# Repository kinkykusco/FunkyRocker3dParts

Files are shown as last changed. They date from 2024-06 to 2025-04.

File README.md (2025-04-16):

# Overview

The Funky Rocker (FR for short) is a DIY sex rocker.  [The plans are for sale from the designer here for a fair price.](http://www.funkyrocker.com)  The FR is a quality design, but is definitely designed without much regard to making it easy to build, or in keeping costs down in terms of parts. The original FR plans require a high degree of accuracy in woodworking, which can be extra challenging with the smaller parts. I switched many of the parts to being 3d printed rather then cut from MDF. After eight months and much use, the 3d printed parts have held up great.  Below are a couple photos of my finished rocker - can you tell which parts are 3d printed? 
<br>
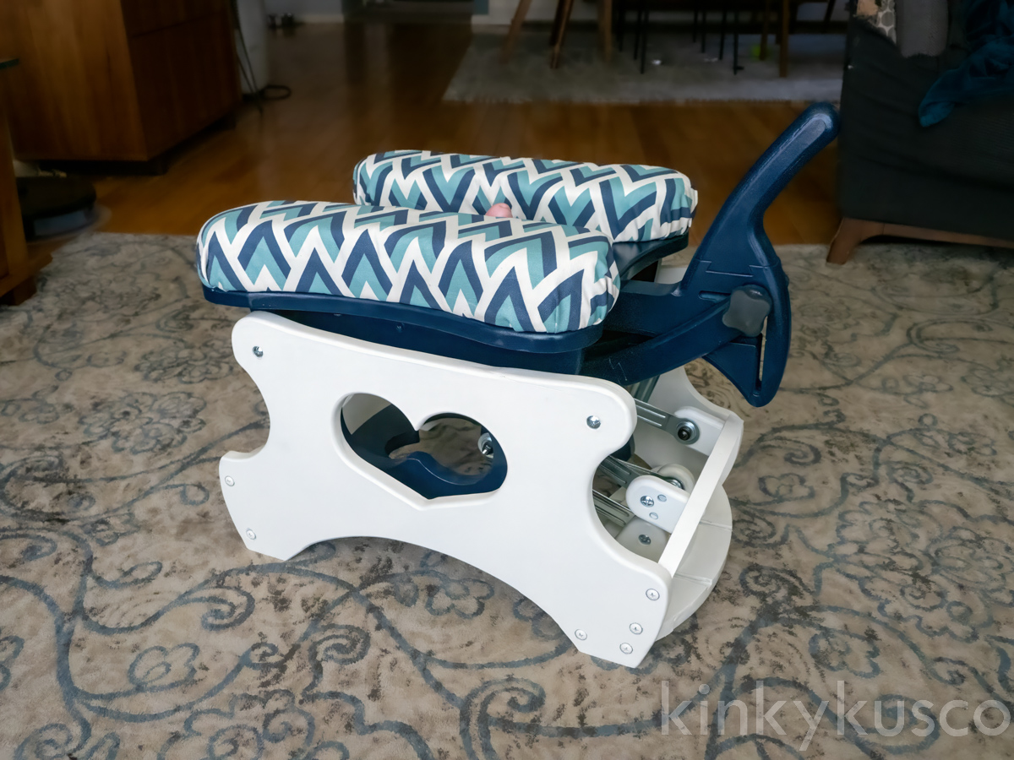
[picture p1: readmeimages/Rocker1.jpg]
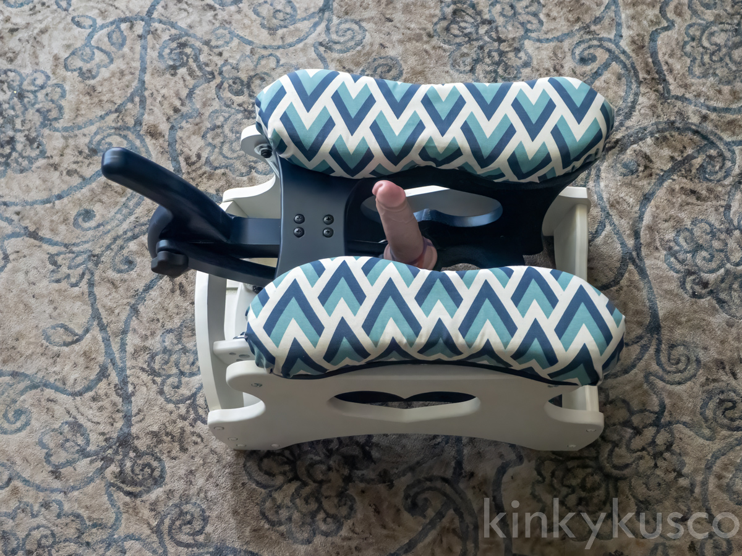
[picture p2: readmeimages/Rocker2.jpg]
 

## Important Notes

My 3D models are not intended to replace the purchase of the original FR plans. You will still need the original plans to make the rest of the parts and to understand the overall assembly of the FR.

The FR plans come in english (imperial) and metric.  I am in the US, and used the english plans as the parts were easier to source.  Consequently my 3d printed parts are based off the english plans.  If you're using the metric FR plans, my parts will probably require some modifications to work.

# Contents

| Part # | Part name | Notes |
| ---: | --- | --- |
| 3 | Aft Support | Included cut in two with a dovetail for printing on smaller print beds and gluing together. |
| 5 | Slide Plate | 5,6,7 all combined as one part |
| 6 | Lower Support - Right | 5,6,7 all combined as one part |
| 7 | Lower Support - Left | 5,6,7 all combined as one part |
| 8 | Slide (2x) | Fits into the above part, glue/epoxy optional |
| 10 | Upper Link Support (2x) | Included cut in two with a dovetail for printing on smaller print beds and gluing together. |
| 14 | Mount Link | 14 + 15 combined as one part |
| 15 | Mount | 14 + 15 combined as one part |
| 17 | Handle | Included cut in two with a dovetail for printing on smaller print beds and gluing together. |
| 17 | Handle Modified | Version of Handle without the actual handle. Found it just got in the way. Fits on one plate|
| 33 | Vac-U-Lock adaptor | 3d printed replacements when using the 3d printed version of part 14+15. |
| N/A | Drill Guide | Drill guide for drilling the dowel nut holes on the edge of the MDF. Print upside down. |

## Printing suggestions

For reference I printed all the parts on a Bambu P1S in PLA.  Check the readme in each folder for notes about those specific files.  The stl's were exported in mm. Most of the parts have an obvious side to print towards the bed.  Rounded edges against the bed may not print well unless you allow supports under them.  Otherwise These should print fine without supports, and I would avoid allowing supports into the bolt holes as they can be very difficult to remove.  

For strength, wall count is generally much more effective then infill.  I printed all these parts with a wall count of 6, 20% infill of gyroid or cross hatch.  Consider variable layer height, especially for the handle, as you want the grip portion with small layer lines to make it feel less 3d printed and more comfortable.

I finished the 3d parts with light sanding, then three coats of an automotive "building" type spray primer to mostly fill in the layer lines, finally a couple coats of spray paint to finish.

## Other suggestions based on my build experience

### Minimum tools required to build the Funky Rocker:

- Router
- Jigsaw
- Drill (bits required: 13/32, 5/16, 17/64 (or 1/4, and then widen slightly/expect the bolt to fit tight), 5/8 (with as flat a drill head profile as possible - no spade bits, etc)

### Tools which will make it much easier/more accurate:

- Scroll or Band saw
- Drill press
- 3d printer

I printed the plans full size and used scotch spray mount to glue the templates to the mdf - it stuck ok, sometimes the paper would lift up and bind under the jigsaw feet.  Use a nail to indent exactly where a hole must be screwed to increase accuracy.  A drill press is going to get the best accuracy with your drill holes, but I was able to free hand it with a drill just fine, during assembly I needed to increase the diameter of a couple of holes to accomidate some inaccuracy, but it was minor and did not effect the final build strength. Apply painters tape to your drill bits to mark the depth of the cut, or use a drill bit stop collars.

Some of the parts have long flat edges (base left and right, glider left and right are the important ones).  plan to use the factory straight edge on the MDF for those flat portions to get a perfectly straight edge.  I did the same with the Forward Lower Support so I could route the channels perpendicular as required.  It's imperative the channels are parallel to each other so the slide plate can slide forward and back, so take care to route those channels very accurately.

I cut my MDF parts out with a jigsaw.  I found the Diablo brand "Scroll Cut wood" blades worked best, but even so the blade will bend a bit around sharp corners leading to a non perfect 90 degree edge.  This was ok with me, but if not acceptable to you, a scroll or band saw is going to be necessary.

Many of the parts call for a larger diameter shallow depression around the bolt holes.  This allows the bolt or receiver head to sit flush.  The only part where these are a necessity is the top of the seat, so the cushions can sit flush.  Otherwise they're entirely for looks.  In hindsight I would have just skipped them, the bolts are visible either way.  

You need to cut the 1/4" threaded rod.  To do so without totally screwing up the thread, [this method I found on familyhandyman.com works well](https://www.familyhandyman.com/article/cutting-threaded-rod/).  The parts list comes with quite a few extra bolts so no harm if you scratch up a few while cutting the rod.  The plans give an approximate rod length for each application which I found too long. Before you assemble the entire bench for the first time, assemble each part assembly which uses a threaded rod by itself with the uncut rod, find the right length, then take it apart and cut the rod.

When you assemble the bench, attach the glider arms to the inner bench section, then place the bench inside the frame and attach the arms to the frame.  If you attach the arms to the frame first, you cannot get the screwdriver in to attach the arms to the inner bench.

# Updated parts list:

Below is the parts list from FR updated to take into account changes from the 3d printed parts, along with some swaps I made.  Mostly I changed some parts to use black hardware when possible, and tried to match materials to prevent galvanic corrosion, what little a project like ths might have, anyway.  My parts list comes out a bit cheaper, but that's almost entirely because you don't need to buy the Vac-u-lock adaptor anymore.

| FR Part # | Qty | 3d print qty | Part name | Cost  | Cost 3d printed | Source | Notes |
| ---: | --: | --: | --- | ----- | --- | --- | --- |
| 20 | 8 | 8 | Glider Bearing Arm | 69 | 69 | [patio furniture rehab](https://www.patiofurniturerehab.com/product/30906/) | Search for "Glider Bearing arm 30-906". There are many online suppliers, while this one was the cheapest I could find when I purchased, that may no longer be the case. |
| 21 | 12  | 12 | Steel Binding Barrels | 16.01 | 16.01 | [McMaster](https://www.mcmaster.com/98002A985/) | |
| 22 | 4 | 0 | 1/4"-20, 1/2" long round head screw | 11.81 | 0 | [McMaster](https://www.mcmaster.com/92224A221/) | |
| 23 | 24  | 20 | 1/4"-20, 1" long truss head screw | 7.43  | 7.43 | [McMaster](https://www.mcmaster.com/92224A225) | |
| 24 | 34  | 30 | 1/4"-20, 2" long truss head screw | 18.62 | 18.62 | [McMaster](https://www.mcmaster.com/92224A230/) | |
| 25 | 17  | 9 | Threaded insert 1/4-20 | 16.28 | 16.28 | [McMaster](https://www.mcmaster.com/92105A675/) | |
| 26 | 34  | 30 | Dowel Nut for wood | 20.56 | 20.56 | [McMaster](https://www.mcmaster.com/90835A200/) | |
| 27 | 18  | 18 | Flat washer | 11.88 | 11.88 | [McMaster](https://www.mcmaster.com/93785A815/) | |
| 28 | 4 | 4 | Locknut | 5.08  | 5.08 | [McMaster](https://www.mcmaster.com/97135A414/) | |
| 29 | 1 | 1 | threaded rod 1' | 6.49  | 6.49 | [McMaster](https://www.mcmaster.com/94210A003/) | |
| 30 | 4 | 4 | Ball bearing flanged | 30.08 | 30.08 | [McMaster](https://www.mcmaster.com/6383K214/) | |
| 31 | 2 | 2 | Four-arm comfort grip knob | 7.14  | 7.14 | [McMaster](https://www.mcmaster.com/2454K28/) | |
| 32 | 1 | 1 | Clamping handle with threaded stud  | 16.15 | 16.15 | [McMaster](https://www.mcmaster.com/5720K12/) | |
| 33 | 1 | 0 | V-L toy adapter | 32 | 0 | [vac-u-lock.com](https://www.vac-u-lock.com/item/61676/Vac-U-Lock-Vibrating-Remote-Black-Plug-w-Snaps.html) | |
| 34 | | | Bearing Grease | | | | Honestly if you need this immediately I'm real jealous of how much you're using your rocker. |
| 35 | | | Seat Foam | | | Get from local craft store | |
| 36 | | | Seat Covering | | | Get from local craft store | |
| 37 | | | Felt | | | Get from local craft store | Other option for feet is plastidip... |
| 38 | 4 | 4 | Bumper | | | Get from local craft store | Could also print from tpu... |
| 39 | 8 | 0 | #4 x 1/2" wood screw | 3.36  | 0 | [Home Depot](https://www.homedepot.com/p/Everbilt-4-1-2-in-Phillips-Flat-Head-Wood-Screws-6-per-Pack-23101/202705647) | |
| N/A | | 1 | superglue or plastic epoxy | | 2.68 | [Home Depot](https://www.homedepot.com/p/Loctite-Super-Glue-0-07-oz-Liquid-Clear-2-Pack-Tubes-each-1399963/310182672) | Required if you're 3d printing the cut version of the handle or handlelink, which you probably are unless you have a large bed printer. |

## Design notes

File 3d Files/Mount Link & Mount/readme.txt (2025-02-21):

Mount and MountLink are the original FunkyRocker design of those parts, requiring the VL toy adaptor to be purchased.  I included these just in case you already own the vac-u-lock adaptor.

MountAndMountLinkScrew is a replacement for those two which skips needing the vac-u-lock adaptor to be purchased, because it has an m18 female screw adaptor for attaching the following to:

FlatMountScrew is a flat plate for suction cup dildos, along with edge clips for tying a dildo on.  Use this if you're wanting to use the rocker with a non vac-u-lock dildo.
VLAdaptor and VLAdaptorTall are two Vac-U-lock adaptors meant for the Screw.  I have found that VLAdaptor works great for our vac-u-lock dildo.  

MaleScrewModel is just the screw portion of an adaptor, to make it easy to create your own whatever to go on top of the mount.  You can join this part directly to anything else in your slicer to easily create different adaptors. 

Handle is a handle with the m18 female threaded part, so you can take your dildo off the funky rocker and use it handheld easily.  

---

Print any part with the screw section (male or female) aligned on the z axis (upwards).  Also print the screw section with small layer height. Doing both will keep the screw geometry as accurate as possible.  The screw parts already have been modified to account for the inaccuracy of FDM printing by loosening their tolerance so no further modification should be required. 

The VLAdaptor/VLAdaptorTall should be printed with at least 8 walls or more, you want them to be very strong and generally walls increase strength more then increased infill.  

If you are expecting your rocker to get used vigorously or for a lot of force to be put onto the insertable, increase the wall count and infill to strengthen the adaptor as necessary.  You can also slightly angle the adaptor something like 10-20 degrees off it's axis, to inscrease the strength at critical join areas like where the screw ends and the flared base of the adaptor begins.  This reduces the chances of it snapping here, without compromizing the geometry of the threads, at the cost of increased supports.

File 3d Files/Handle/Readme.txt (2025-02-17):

Included are two different handles.  "Handle" is the original, taken from the funky rocker plans.  It comes in two parts, precut with a dovetail for gluing so it fits on most build plates.  I suggest variable layer height so you can get a smoother surface of the handle itself.

The second option, "Handle Modified", gets rid of the handle portion of the part.  In practice, we found she doesn't need the handle at all, she just moves the rocker forward and back with her legs.  Her hands are more likely to be busy elsewhere.  Rather, when we use the chair together, the handle was just causing problems, as it limited how closely I could sit in front of her.  By eliminating the protrusion, we find the rocker more fun to use as a couple.  It also makes it slightly smaller, so easier to hide away in a closet or box. Finally, it's small enough to fit on a 256mm x 256mm build plate in one go. I highly recommend using Handle Modified over handle.

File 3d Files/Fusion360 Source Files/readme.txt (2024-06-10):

Handle.f3d contains just the handle
HandleLink.f3d contains just the handlelink
MountandVLAdaptor.f3z contains the mount and all the VLAdaptor designs
FunkyRockerParts.f3d contains all the other parts

If you are going to modify these files, please accept my apology if the models are difficult to use, I did not design them with the expectation of sharing them so I was fairly lazy with naming conventions and general good design principles, I just mocked them up quickly.

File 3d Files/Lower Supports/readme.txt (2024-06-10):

While the individual lower supports are included here, if 3d printing I suggest using the "lower support and slide" located in the slide folder instead, as it integrates the 
lower supports into the slide plate as one unit.  Then you don't need to print these at all.

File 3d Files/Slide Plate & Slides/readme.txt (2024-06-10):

Print 1x IntegratedSlideandLowerSupport and 2x SlidesForIntegrated.  Glue the SlidesforIntegrated onto the bottom of the Integrated Slide. 

 I suggest waiting to glue until you've made the forward lower support, and use that to align the slides during the glue up so that the slides align as expected.

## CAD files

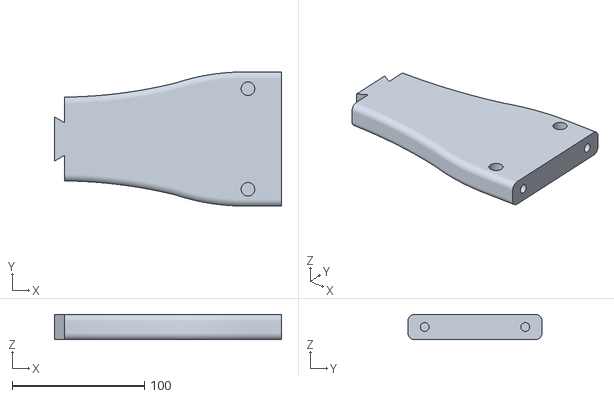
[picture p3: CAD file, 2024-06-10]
3d Files/Aft Support/AftSupportCutA.stl
171.9 x 101.6 x 19.0

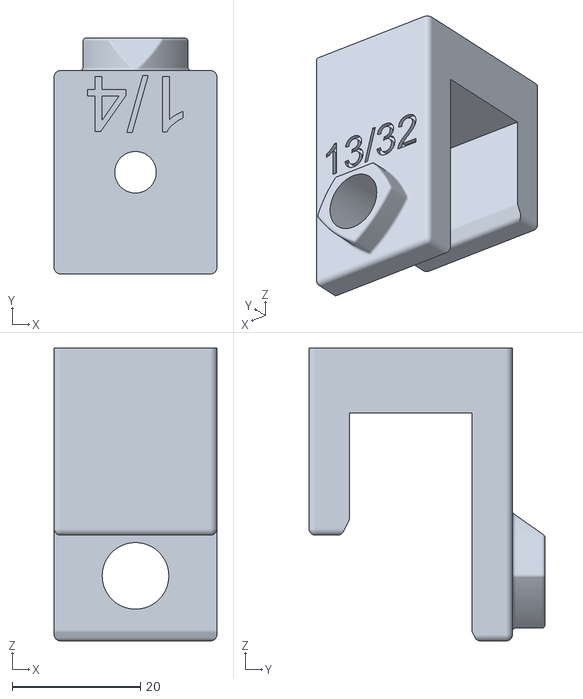
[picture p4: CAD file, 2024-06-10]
3d Files/Drill Guide/DrillGuide.stl
25.4 x 36.8 x 45.7

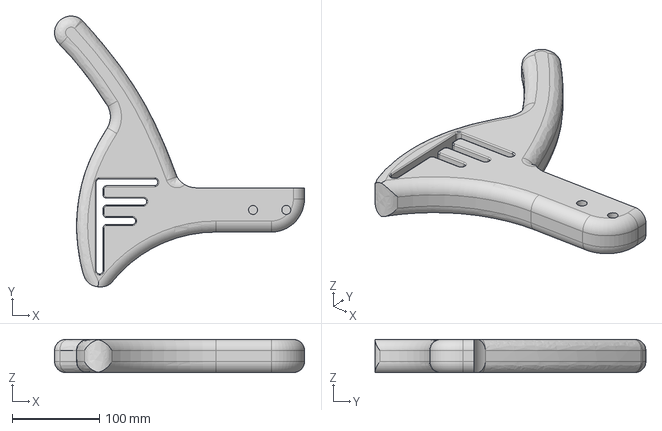
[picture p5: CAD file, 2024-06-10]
3d Files/Handle/Handle.step
286.7 x 310.6 x 38.1 mm

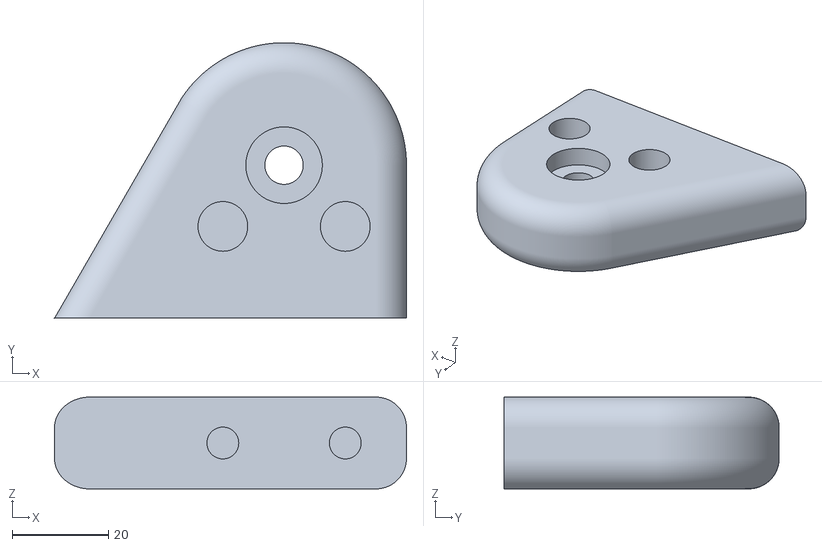
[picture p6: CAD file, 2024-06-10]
3d Files/Lower Supports/LowerSupportRightSide.stl
73.0 x 57.1 x 19.0

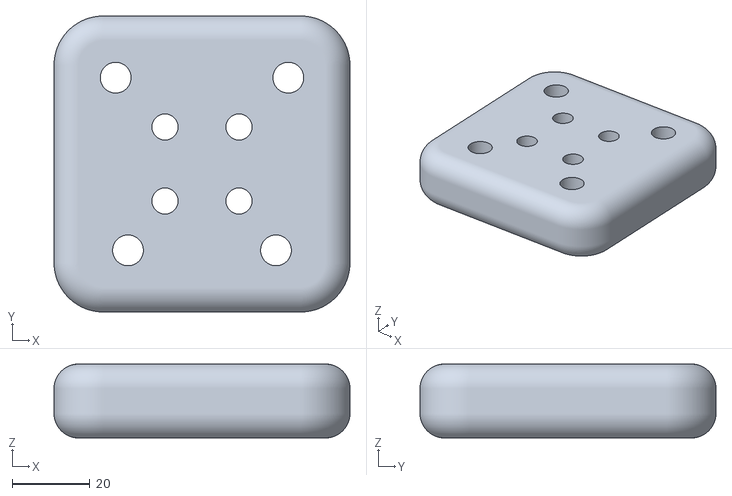
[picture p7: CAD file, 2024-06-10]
3d Files/Mount Link & Mount/Mount.stl
76.2 x 76.2 x 19.0

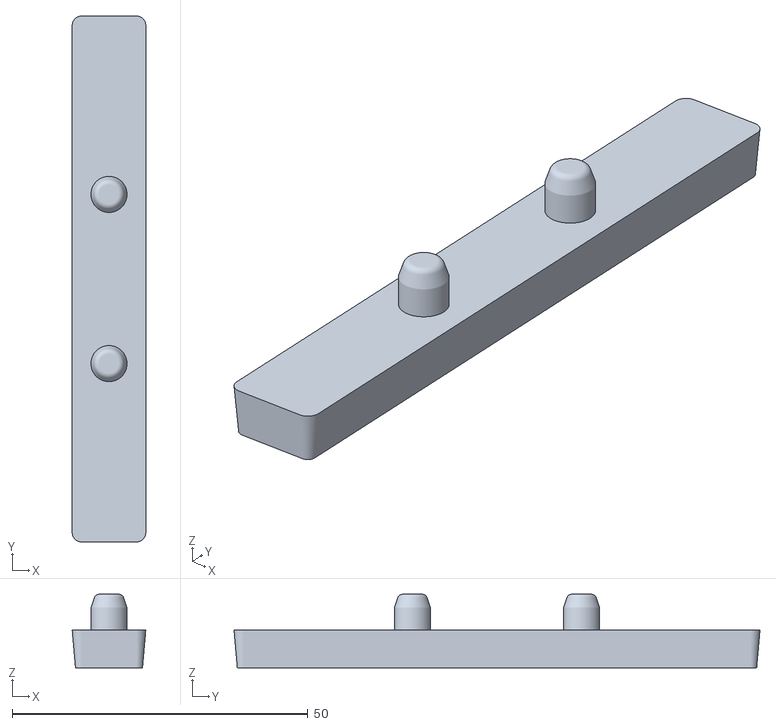
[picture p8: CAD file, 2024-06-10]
3d Files/Slide Plate & Slides/SlidesForIntegrated.stl
12.4 x 88.9 x 12.4

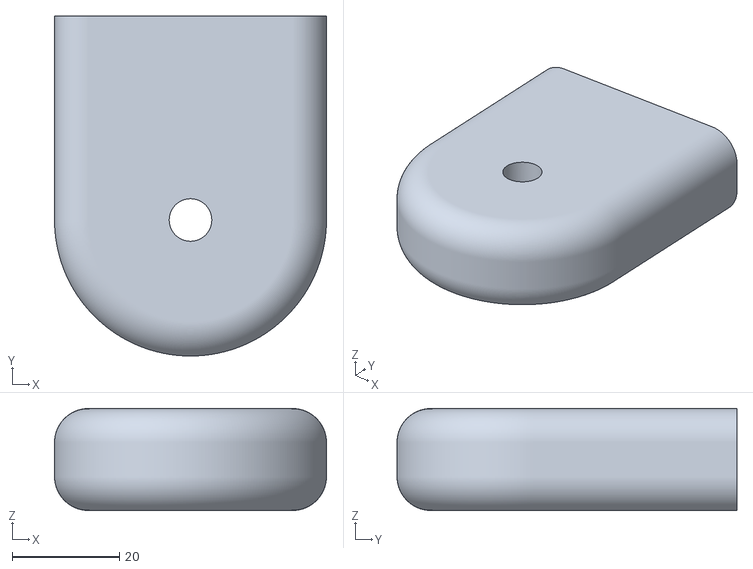
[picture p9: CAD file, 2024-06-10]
3d Files/Upper Link Support/UpperLinkSupport.stl
50.8 x 63.5 x 19.0

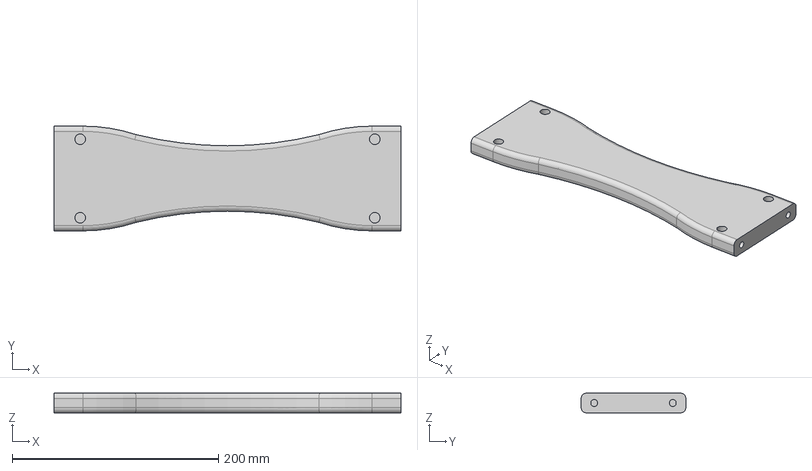
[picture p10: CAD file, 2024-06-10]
3d Files/Aft Support/AftSupport.step
336.5 x 101.6 x 19.0 mm

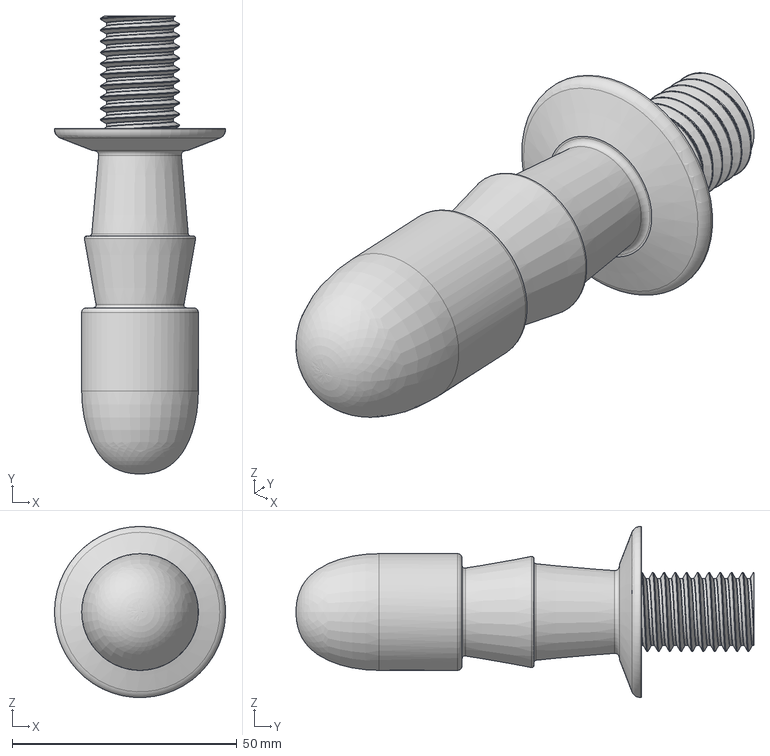
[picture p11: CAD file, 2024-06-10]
3d Files/Mount Link & Mount/VLAdaptor.step
38.1 x 102.0 x 38.1 mm

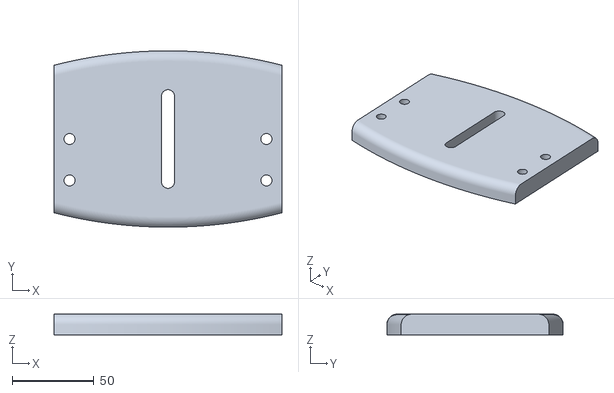
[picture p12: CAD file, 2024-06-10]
3d Files/Slide Plate & Slides/SlidePlateOriginal.stl
139.7 x 108.0 x 12.7

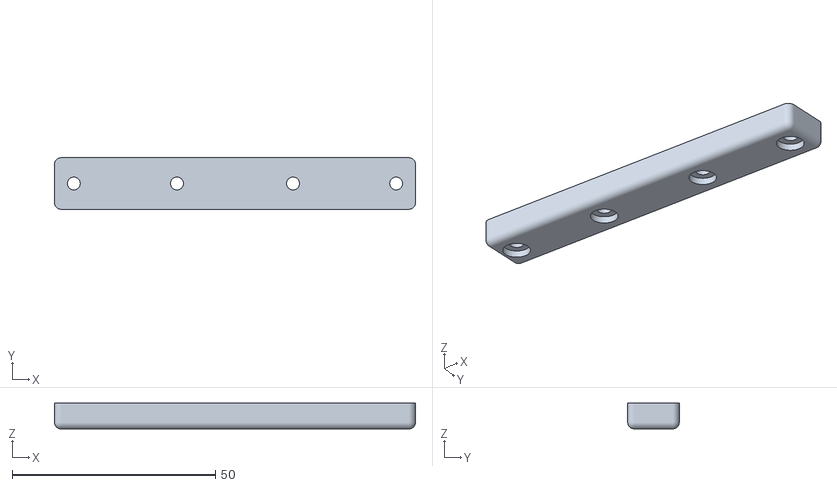
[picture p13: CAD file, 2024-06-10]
3d Files/Slide Plate & Slides/SlideOriginal.stl
88.9 x 12.7 x 6.35

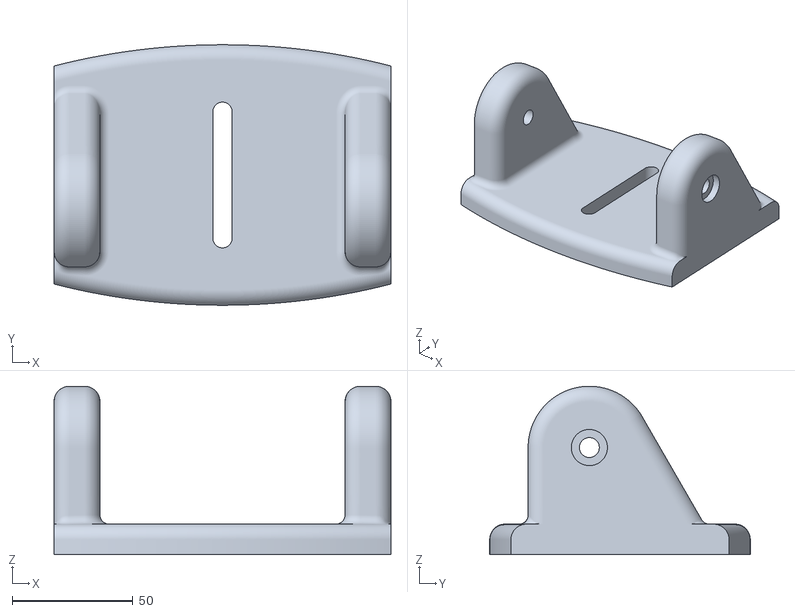
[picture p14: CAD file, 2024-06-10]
3d Files/Slide Plate & Slides/IntegradedSlideandLowerSupports.stl
139.7 x 108.0 x 69.8

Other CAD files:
3d Files/Lower Supports/LowerSupportLeftSide.stl
3d Files/Aft Support/AftSupportCutB.stl
3d Files/Fusion360 Source Files/FunkyRockerParts.f3d
3d Files/Fusion360 Source Files/Handle.f3d
3d Files/Fusion360 Source Files/HandleLInk.f3d
3d Files/Fusion360 Source Files/HandleModified v1.f3d

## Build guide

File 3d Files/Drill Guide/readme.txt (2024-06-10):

Print upside down with many walls (>6).  Should print fine without supports.  

You may want to print two of them.  Over time I found the drill bits slowly widen the guide making it less accurate.  Use one for the first half of the required dowel nut holes, then discard and switch to the second.

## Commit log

2024-06-10 Added all files
    All 3d files and a license file added to respository.
    [AftSupport.step, AftSupportCutA.stl, AftSupportCutB.stl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]
2025-02-17 Add files via upload
    Added HandleModified, a revision on the handle piece, which eliminates the handhold, which we found not necessary for her, and gets in the way for him.
    [HandleModified v1.f3d]
